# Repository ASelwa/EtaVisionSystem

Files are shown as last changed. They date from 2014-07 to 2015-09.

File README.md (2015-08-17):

**EtaVisionSystem**
===============

This repo contains code and documentation for AeroVelo's Eta speedbike vision system.

It includes code for the Arduino Mega, code for the minimOSD, and some documentation as well as datasheets.

####BRANCHES

The _master_ branch contains the most recent updates.

The _BM-2014_ branch is a quick way to access the code ran at Battle Mountain in September 2014. There were several bugs and issues to be addressed, however it still used at road testing several times leading up to 2015.

The _No-Serial-Printing_ branch contains the code ran at Battle Mountain 2014 without serial printing.

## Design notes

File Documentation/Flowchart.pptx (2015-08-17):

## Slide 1

Start

#include

#define

Variables init

Serial ports opened
Pin modes set
GPS init
SD init
ANT setup
calibrate()

void setup()

void loop()

Periodic While Loop

PERIOD milliseconds hasn’t passed

Increment TIME by PERIOD
Save all data to SD card

New GPS data?

Lat, long, alt moving average.
Displacement, distance calculation
Target power (if not simulation mode)
Toggle()
Send profile
Send mode
Send target speed, speed, simulated speed, distance, displacement, battery info, temperature

GPSLost &&
Time passed > 1000 ms?

Time passed > 7000 ms?

GPSLost = true

Not in Simulation?

Reinitialize GPS

Toggle()
Send profile
Send mode
Send target speed, speed, simulated speed, distance, displacement, battery info, temperature

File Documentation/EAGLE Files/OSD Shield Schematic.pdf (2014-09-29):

2014-09-28 9:58 PM f=1.40 /Users/ASelwa/Documents/GitHub/EtaVisionSystem/Documentation/EAGLE Files/OSD Shield.sch (Sheet: 1/1) VIN P$1 | PIN P$2 | GNDIN P$3 VOUT P$4 | POUT P$5 | GNDOUT P$6
BLK | P$12
GND | P$11
5V | P$10
RX | P$9
TX | P$8

OSD1

GRN P$7

### VIN P$1

### PIN P$2

### GNDIN P$3

### VOUT P$4

### POUT P$5

### GNDOUT P$6

BLK | P$12
GND | P$11
5V | P$10
RX | P$9
TX | P$8

OSD2

GRN P$7

# 1 P$1 2 P$2 3 P$3 SH P$4

CCAM1

# 1 P$1 2 P$2 3 P$3 SH P$4

CCAM2

1 P$1

2 P$2

# 3 P$3 SH P$4

CVOUT1

1 P$1

2 P$2

# 3 P$3 SH P$4

CVOUT2

1 P$1

2 P$2

# 3 P$3 SH P$4

CTEL

TX
RX

DGND

AGND1
VIN1

5V-1

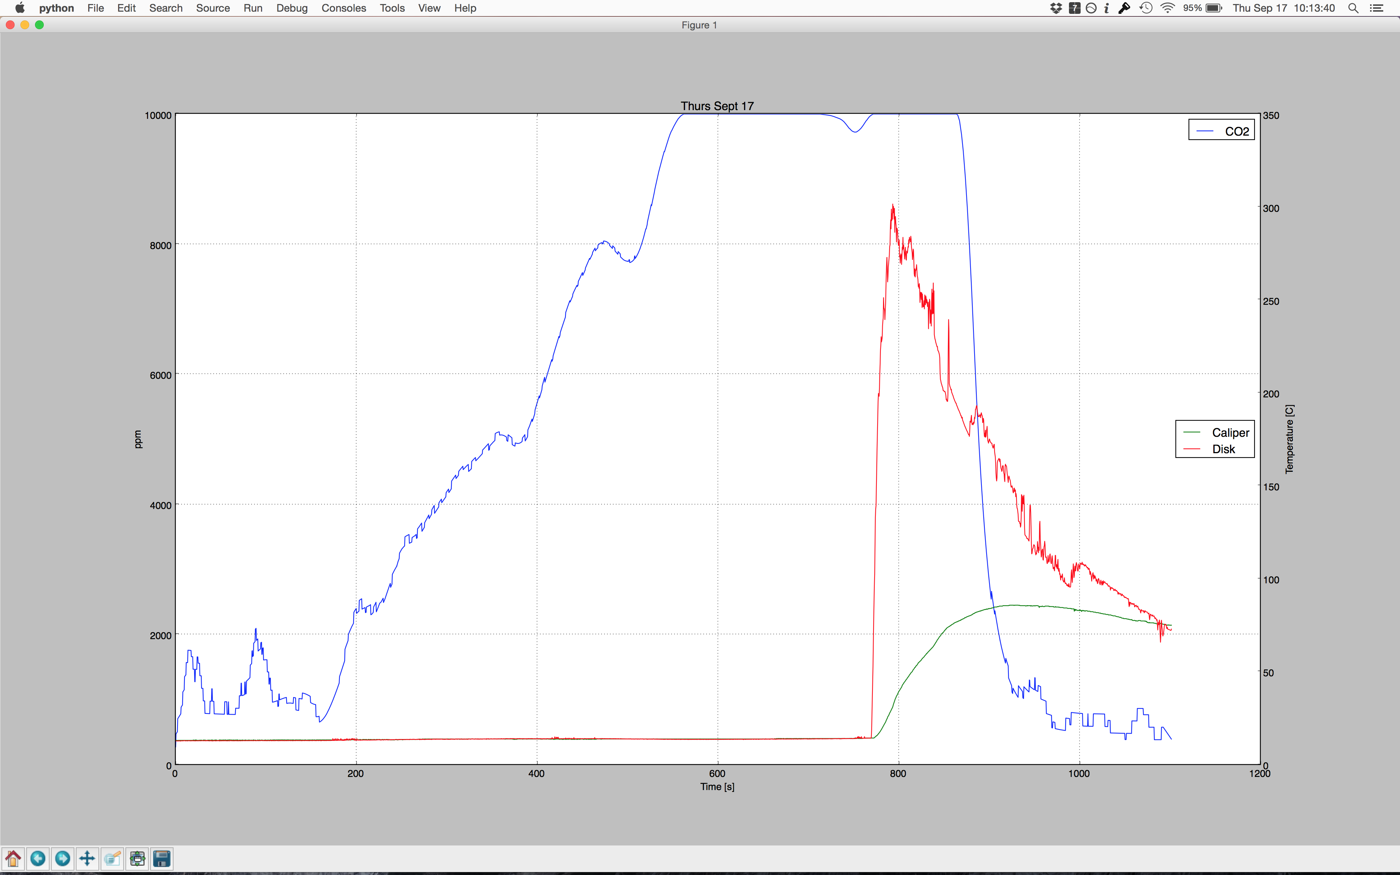
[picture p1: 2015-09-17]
BM 2015 Logs/17 Sept Thursday/CO2 and Temperature.png

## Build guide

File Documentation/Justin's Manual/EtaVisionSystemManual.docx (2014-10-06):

# Eta Vision System Manual

# Introduction to Eta’s Code Structure

The code for Eta’s vision system is divided into two main directories: HPV_ArduinoMega and HPV_OSD. A wealth of standard and custom libraries also support the system’s functioning. With the exception of ArduCam_Max7456 and GPS_UBLOX, there should be no need to modify any of these libraries.

## HPV_ArduinoMega

HPV_ArduinoMega contains files defining the system’s logic. The Arduino streams data from peripheral devices, calculates values of interest, and sends the data to the OSD. Currently, the peripherals supported are:

- ANT+ receiver configured for power pedals, crank torque frequency pedals (e.g. Todd’s SRM), and heart meter
- uBLOX GPS
- Battery meter
- Temperature sensor
- SD card reader

### HPV_ArduinoMega.ino

This is the central processing centre of the system. The setup initializes all the peripherals and pins and calls the calibration function to calibrate the pedals. The main loop receives data from the peripherals, calculates values of interest, and sends these values to the OSD chip via its serial link. In general, data is sent whenever a new message is received from the GPS or the ANT+ receiver. This file also takes care of most of the logging activity, writing values every two seconds to the SD card.

Every time the GPS sends data, or every one second if the GPS is not available, the program will check if the profile toggle button has been pushed. If so, the program will load the next profile.

Notes:

- Most of the variables to display are sent to the OSD when there is a GPS update. Since the GPS may not always be available, there are two lengthy cases containing nearly identical code. One block will execute whenever the GPS updates with a new message while the other block will take over if the Arduino loses its GPS connection. Remember to copy any code you add into both blocks (if applicable).
- The update frequency of logs can be set by changing PERIOD in ANT_interface.h
- Anything related to the START variable seems to have been deprecated

### Ant_interface.cpp

This file contains functions for communication with the antenna. No changes should be necessary to the current code.

### BatteryCheck.ino

This file contains functions to measure the temperature and battery voltage.

### GPS_Func.ino

This file contains logic related to the calculations done with GPS coordinates.

### SD_Func

This file contains functions to perform basic write and read operations.

### TargetSpeed_Func

The functions in this file carry out a variety of tasks not necessarily related to calculating the target speed. The main function is toggle(), which takes care of loading new profiles and switching between real-time and simulation modes. There are also functions to calculate target speed and target power.

# Logging

Currently, there are two logs created for each run of the program. The “LOG” file is a general log that is written to at regular intervals and contains information from all of the peripherals connected. This interval is defined by the PERIOD variable. The contents that are logged can be modified by changing the print commands at the end of loop() in HPV_ArduinoMega.ino. The column headers are specified in setup() of the same file.

The “SLG” file is written to whenever non-duplicate power meter messages are received from the SRM. The contents that are logged can be modified by changing the print commands at the end of loop() in HPV_ArduinoMega.ino. The column headers are specified in setup() of the same file.

Different types of logs from the same run will always have the same number in their file name.

# Programming the OSD

Note: Do not use the OSD configuration GUI. It seems incompatible with the way Eta’s OSD is currently set up and it does not support custom panels.

To program the OSD, connect it to the computer via an FTDI-USB converter. Upload the code through the Arduino IDE, making sure that the board is set to “Arduino Pro or Pro Mini” and the processor is set to “ATMega328 (5V, 16 MHz)”.

## Adding a Display

To add a variable to display onto the screen:

1. Define an ID at the beginning of OSD_SLIP.h and in HPV_ArduinoMega.ino
2. Perform calculations in the main loop of HPV_ArduinoMega.ino
3. Send the value in the main loop via SlipPacketSend()
4. Add an extern variable declaration in OSD_SLIP.cpp
5. Add the regular variable declaration in HPV_OSD.ino
6. Add a case to OSD_SLIP.cpp to extract the value from the buffer and assign it to the variable from steps 4 and 5
7. Add a panel function to OSD_panels_HPV.ino
8. Call the function in writePanels() (also located in OSD_panels_HPV.ino)

## Parameters of Interest

Baud rate: TELEMETRY_SPEED, ArduCAM_OSD.ino

Start-up speed: BOOTTIME, ArduCAM_OSD.ino

# Elevation Calculations

Elevation data is stored using a 2D array of distance and elevation pairs. To keep the data structure small, a few key points along the track were chosen so that linear interpolation could be used for a reasonable estimate of the elevation anywhere along the track. This data can be found near the beginning of simulation.cpp.

The change in elevation cannot be found without first knowing the distance travelled. The distance travelled cannot be known without calculating the net energy added to the bike, but part of this net energy is due to the change in elevation. This circular dependence necessitates an iterative algorithm.

1. First, elevation is ignored. Power, velocity, and distance travelled are calculated.
2. The distance travelled is used to find the change in elevation. Power is recalculated with the power of the elevation change included.
3. Velocity and distance calculations are repeated with the new power value.
4. The elevation change is recalculated. Power is recalculated.
5. Velocity and distance are recalculated.

And so on. Each iteration should result in a closer and closer approximation to the actual distance. The process stops after a maximum of ten iterations, or when the difference in elevation power is less than 1 W, whichever occurs first.

# SRM Data

The SRM sends messages to the antenna at a non-configurable rate of every half a second. While the bike is being pedalled, the contents of the power messages will only update every full revolution. Any messages sent before the next full revolution will be a duplicate of the previous.

# Common Tasks

## Add a speed profile

Create a new file on the SD card called “PF##” where the pound signs are the next unused profile number.

Note: Numbering must begin at 01 and all subsequent profile numbers must be consecutive. The program will stop looking for profiles if it cannot find a profile with the next consecutive number.

The first argument is the profile name. The name should be a maximum length of 10 characters and cannot contain spaces. A profile name longer than the limit will be truncated when it is displayed. The next six arguments are the coefficients for the polynomial approximation in order of highest power (degree 6) to lowest (constant term). Each argument must be separated by a space.

## Change the target power profile

The target power profile currently uses a simple linear equation to find the target value. The starting and ending targets are defined as preprocessor variables POWER_START and POWER_PRE_SPRINT. To change the method of calculation, modify functions calcPower() and calcDisplacePower()in TargetSpeed_Func.ino.

## Set the finish line coordinates

Edit the file on the SD card called “FinCoord.txt”. The first argument is the latitude (in degrees), the second is the longitude (in degrees), and the third is the altitude (in metres). Each argument must be separated by a space.

# Troubleshooting

## No calibration data is received (display will only read “Waiting”)

This is likely a problem with the antenna. If certain antenna pins short, the antenna will not work until the short is removed and the antenna is reinitialized.

1. Unplug and plug the antenna. Ensure nothing is shorting the pins. Restart the program.
2. Replace the antenna with the backup.
3. Measure the three baud rate selection pins while the Arduino is powered and ensure their logic levels match the ones specified for the baud rate used in the program (see Antenna Datasheet.pdf).
4. Comment out the call to calibrate() in HPV_ArduinoMega’s setup(). Run the program using the serial monitor. If there are no ANT+ messages received after the ANT+ setup has complete, the problem is definitely with the antenna.

At this point, if the problem persists, switch to a back-up system and try again later.

## Power, cadence, distance and heart rate displays freeze

These are all dependent on the antenna. See above.

The power meter will automatically shut off after a specified period of no activity (around 2 minutes). After this time, the program will stop calculating new values.

## GPS not available

1. Check that the device is getting power (red LED should be lit).
2. Restart the system.
3. Try the old GPS. If it works, the new one is likely damaged or misconfigured.
4. Start U-Center and plug the GPS into the computer. Ensure the correct messages are being sent, the baud rate is configured correctly, and the message rate is reasonable. (Refer to the GPS configuration section). If U-Center can’t communicate with the GPS, it may be damaged. Use the backup GPS.

## OSD text flickers on screen

1. Ensure the OSD wire connections are stable and nothing is touching the OSD chip.
2. Ensure any calls to OSD.clear() are controlled appropriately (do not attempt to call the function without a time delay).
3. Ensure the display and OSD chip are both set on NTSC mode (see OSD section).

## A Value jumps to an extremely large number

This is most likely caused by a division by zero (and not some hidden modification of variable values or overwriting memory where it shouldn’t be overwritten). Check any calculations related to the variable and ensure that undefined operations cannot occur.

# Known Issues

## Arduino peripherals (e.g. GPS) stop working after uploading new code

### Cases

Uploading the code using Justin’s laptop running Arduino 1.5.5 (older, no longer supported), the code works as expected. When identical code is uploaded using Steven’s laptop running Arduino 1.0.5 (newest version of the 1.0 series), the GPS will not initialize.

### Analysis

Compiling on different versions of the IDE (or possibly on different computers) may break the code. In the given case, it seems to be related to the pre-processor variables that detect what Arduino board the GPS is running on (see GPS_UBLOX_Class::Init in GPS_UBLOX.cpp). More testing is required to determine the cause of this. We suspect this problem can be fixed by removing the pre-processor variables, forcing the code to assume an ATMega board.

## Serial Buffer Overflow – Solved

### Cases

The ANT+ serial will occasionally receive corrupted messages that can be up to 255 bytes long. This is highly dangerous, as the ANT+ buffer is only large enough to support messages up to 64 bytes. (In theory, no messages should be above 9 bytes in length.) Additional bytes will write into adjacent memory, overwriting any variables that may be stored there. This behaviour is completely undefined.

### Analysis and Solution

It seems as though these large, “cancerous” messages are actually composed of a few 9-byte messages repeated many times.

The code relies on a sync byte (0xA4 or 0xA5, although in practice it always seems to be 0xA4 and the code ignores 0xA5 for extra security) to identify the beginning of a message. The program is usually fine at synchronizing with the ANT+ serial, but sometimes it misinterprets a 0xA4 that is part of a message payload to be the sync byte of a new message. It will then assume that the following byte is the message length, causing this error.

A check has been put into place in receiveANT() of ANT_interface.cpp to discard the message as soon as the message length byte is greater than 9. This means an overflow should never occur with antBuffer.

## SD card contains strange files

### Cases

The SD card is susceptible to corruption. Our testing has shown the following cases:

- A file with the name “ . ■” that Windows Explorer thinks takes up around 4GB of drive space. Pulling up the Properties window, however, shows that it is an empty (0B) file.
- A “ghost” file that takes up no space and cannot be deleted (deleting is successful, but refreshing the directory will cause the file to reappear).

### Analysis

This problem likely stems from the fact that the SD card can be removed at any time, including during a write operation. There is a library function to initialize the SD card, but no function to disconnect safely from the SD.

## Simulation – Solved???

### Cases

The simulate function risks dividing by 0, which may cause undefined behaviour. On the Arduino, variables will become infinity or NaN (not a number). On the OSD, they may display as garbage values. As soon as velocity and/or distance become either of these values, they will not recover.

### Analysis and Solution

Steps have already been taken to prevent floating point calculations from ruining the program. Guards are present in many simulate() calculations to attempt to handle unreasonable values, and simulate() includes a final check that will abort the current iteration without updating any of the values if any variables become infinite or undefined. Recent testing and logging have not revealed any problems with infinite or undefined variables; however, they have also not revealed any cases in which undefined variables were actually caught and handled gracefully. Therefore, it is not known if the current security measures are effective.

## Shorting – Solved

### Cases

When standoffs were still installed on the box and the Arduino was powered without properly locking it in place, the board heated rapidly, becoming hot enough to burn the epoxy.

### Analysis and Solution

We speculate that one of the standoffs came into contact with the Vin pin on the bottom of the Arduino and shorted it by conducting across the carbon fibre board. Never run the circuit while the Arduino is sitting on a conductive surface.

The nature of the problem could have been avoided by replacing the standoffs with foam or another insulating material. The box is now taped to prevent this from happening in the future.

## OSD shows rapidly flashing garbage numbers in place of meaningful ones – Solved

### Cases

Whenever a value is rapidly written to the OSD (no explicit time delay between writes), the value flickers to random numbers.

### Analysis and solution

The reason for this is unknown, but the problem can be solved by ensuring an adequate delay between write operations.

# Miscellaneous Notes

## Forward Declarations

- Arduino automatically generates forward declarations for functions. It is therefore never necessary to do so for most functions.
  - Exceptions include functions with function pointers as parameters, default arguments, and functions declared in a namespace or class. Manual declarations will be necessary.

## Multi-file Programs

- Arduino (.pde and .ino) files do not work like regular .c or .cpp files. The Arduino compiler concatenates all Arduino files in the same folder into one compilation unit. (C and C++ files are treated as separate compilation units.) The concatenation begins with the main file (which shares the folder name), followed by the other Arduino files in alphabetical order (not verified, widely accepted). Therefore, for Arduino files in the same folder:
  - Include statements are only necessary in the main file
  - The static keyword will not restrict variable scope to only the local Arduino file
  - Global variables in one file do not have to be declared as extern in another to be used
  - Regular variable scope rules still apply. A global variable declared in “B.ino” cannot be referenced in “A.ino” because A will concatenated before B.

## SD Card

- Arduino cannot log files with names longer than 8 characters (FAT 8.3 standard (http://arduino.cc/en/Reference/SDCardNotes)).
- Arduino capitalizes all letters in file names when creating a file.

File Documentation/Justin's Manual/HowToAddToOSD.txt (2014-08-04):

To add a variable to display onto the screen:

1. Define an ID in OSD_SLIP.h and in HPV_ArduinoMega
2. Perform calculations/read from ANT in main loop of HPV_ArduinoMega
3. Send value in main loop via SlipPacketSend
4. Add an extern variable declaration in OSD_SLIP.cpp
5. Add the regular variable declaration in HPV_OSD
6. Add a case to OSD_SLIP.cpp to extract the value from the buffer and assign it to the variable from steps 4/5
7. Add a panel function to OSD_panels_HPV
8. Call the function in writePanels() (also located in OSD_panels_HPV)

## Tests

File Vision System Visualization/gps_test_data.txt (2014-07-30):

Index	UTC	SoG	Lat	Lon
Unit	time date	m/s	°	°
Count	1344	1344	1344	1344
Age	0	0	0	0
Current	23:08:41.000 07/29/2014	0.01	43.551496	-79.663104
Minimum	22:46:18.000 07/29/2014	0.00	43.535137	-79.663115
Maximum	23:08:41.000 07/29/2014	34.11	43.658515	-79.393437
Average		14.63	43.589041	-79.582394
Deviation		12.37	0.046276	0.084452
0	22:46:18.000 07/29/2014	0.00	43.658515	-79.393437
1	22:46:19.000 07/29/2014	0.00	43.658515	-79.393437
2	22:46:20.000 07/29/2014	0.00	43.658515	-79.393437
3	22:46:21.000 07/29/2014	0.00	43.658515	-79.393437
4	22:46:22.000 07/29/2014	0.00	43.658515	-79.393437
5	22:46:23.000 07/29/2014	0.00	43.658515	-79.393437
6	22:46:24.000 07/29/2014	0.00	43.658515	-79.393437
7	22:46:25.000 07/29/2014	0.00	43.658515	-79.393437
8	22:46:26.000 07/29/2014	0.00	43.658515	-79.393437
9	22:46:28.000 07/29/2014	0.00	43.658515	-79.393437
10	22:46:29.000 07/29/2014	0.00	43.658515	-79.393437
11	22:46:30.000 07/29/2014	0.00	43.658515	-79.393437
12	22:46:31.000 07/29/2014	0.00	43.658515	-79.393437
13	22:46:32.000 07/29/2014	0.00	43.658515	-79.393437
14	22:46:33.000 07/29/2014	0.00	43.658515	-79.393437
15	22:46:34.000 07/29/2014	0.00	43.658515	-79.393437
16	22:46:35.000 07/29/2014	0.00	43.658515	-79.393437
17	22:46:36.000 07/29/2014	0.00	43.658515	-79.393437
18	22:46:37.000 07/29/2014	0.00	43.658515	-79.393437
19	22:46:38.000 07/29/2014	0.00	43.658515	-79.393437
20	22:46:39.000 07/29/2014	0.00	43.658515	-79.393437
21	22:46:40.000 07/29/2014	0.00	43.658515	-79.393437
22	22:46:41.000 07/29/2014	0.00	43.658515	-79.393437
23	22:46:42.000 07/29/2014	0.00	43.658515	-79.393437
24	22:46:43.000 07/29/2014	0.00	43.658515	-79.393437
25	22:46:44.000 07/29/2014	0.00	43.658515	-79.393437
26	22:46:45.000 07/29/2014	0.00	43.658515	-79.393437
27	22:46:46.000 07/29/2014	0.00	43.658515	-79.393437
28	22:46:47.000 07/29/2014	0.00	43.658515	-79.393437
29	22:46:48.000 07/29/2014	0.00	43.658515	-79.393437
30	22:46:49.000 07/29/2014	0.00	43.658515	-79.393437
31	22:46:50.000 07/29/2014	0.00	43.658515	-79.393437
32	22:46:51.000 07/29/2014	0.00	43.658515	-79.393437
33	22:46:52.000 07/29/2014	0.00	43.658515	-79.393437
34	22:46:53.000 07/29/2014	0.00	43.658515	-79.393437
35	22:46:54.000 07/29/2014	0.00	43.658515	-79.393437
36	22:46:55.000 07/29/2014	0.00	43.658515	-79.393437
37	22:46:56.000 07/29/2014	0.00	43.658515	-79.393437
38	22:46:57.000 07/29/2014	0.00	43.658515	-79.393437
39	22:46:58.000 07/29/2014	0.00	43.658515	-79.393437
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

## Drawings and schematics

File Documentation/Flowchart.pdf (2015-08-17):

# void setup()

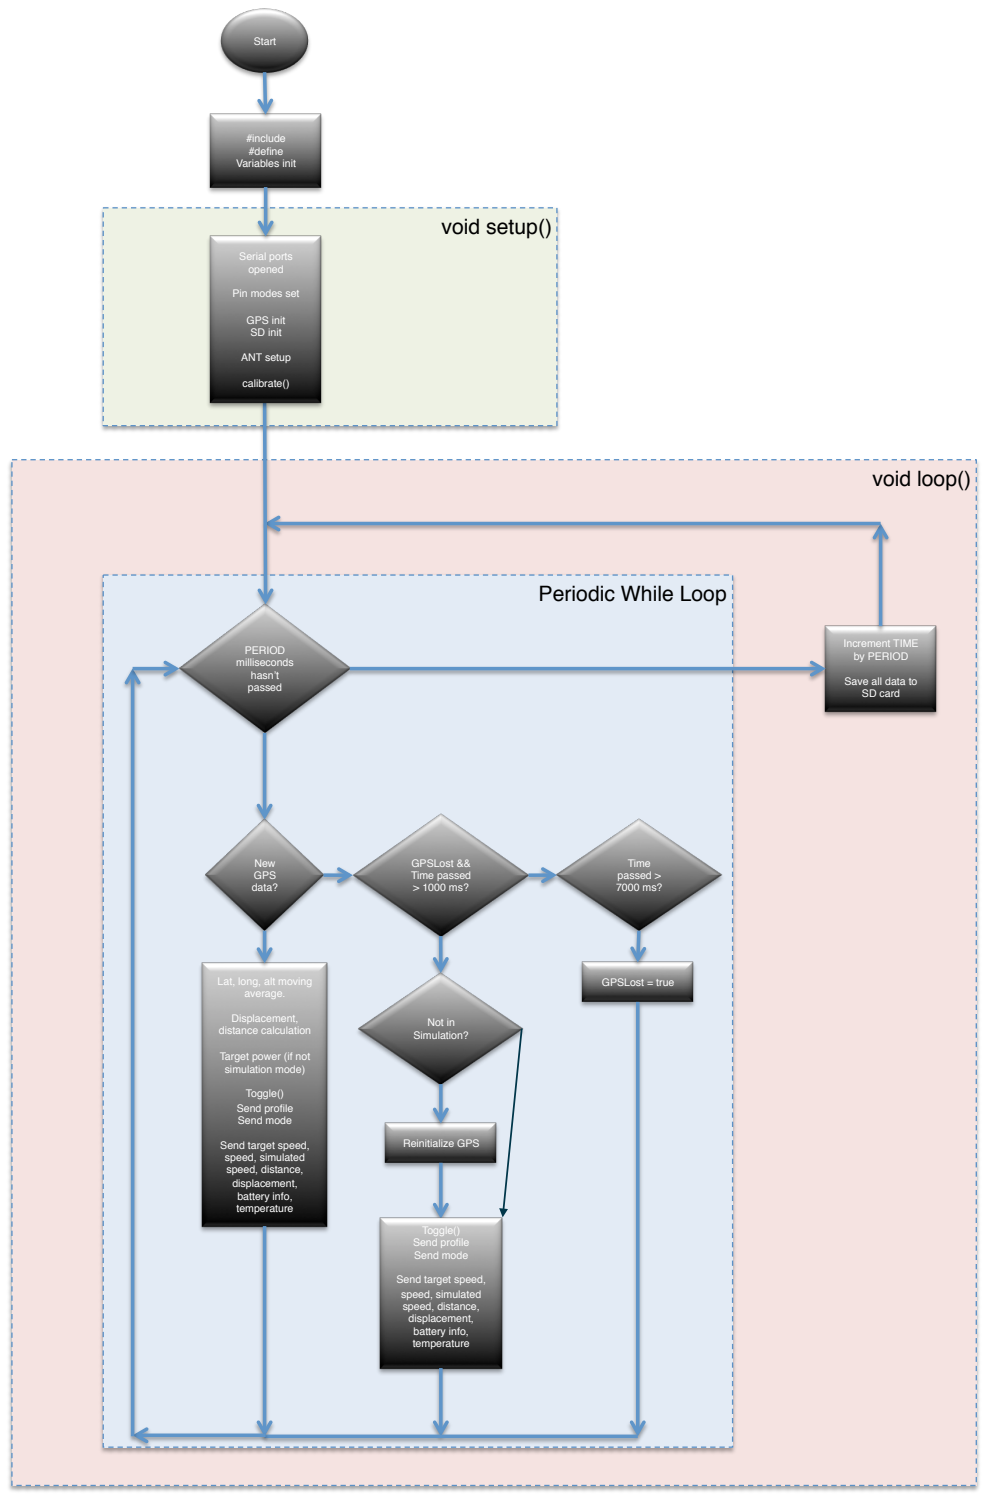
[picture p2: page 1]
void loop(); New GPS data?; GPSLost && Time passed > 1000 ms?; Not in Simulation?; Time passed > 7000 ms?; GPSLost = true; Reinitialize GPS; Toggle() Send profile Send mode; Displacement, distance calculation; Increment TIME by PERIOD; PERIOD milliseconds hasn’t passed; #include #define Variables init; Serial ports opened; GPS init SD init; ANT setup; calibrate(); Start

Pin modes set

Periodic While Loop

Save all data to
SD card

Lat, long, alt moving
average.

Target power (if not
simulation mode)

Send target speed,
speed, simulated
speed, distance,
displacement,
battery info,
temperature

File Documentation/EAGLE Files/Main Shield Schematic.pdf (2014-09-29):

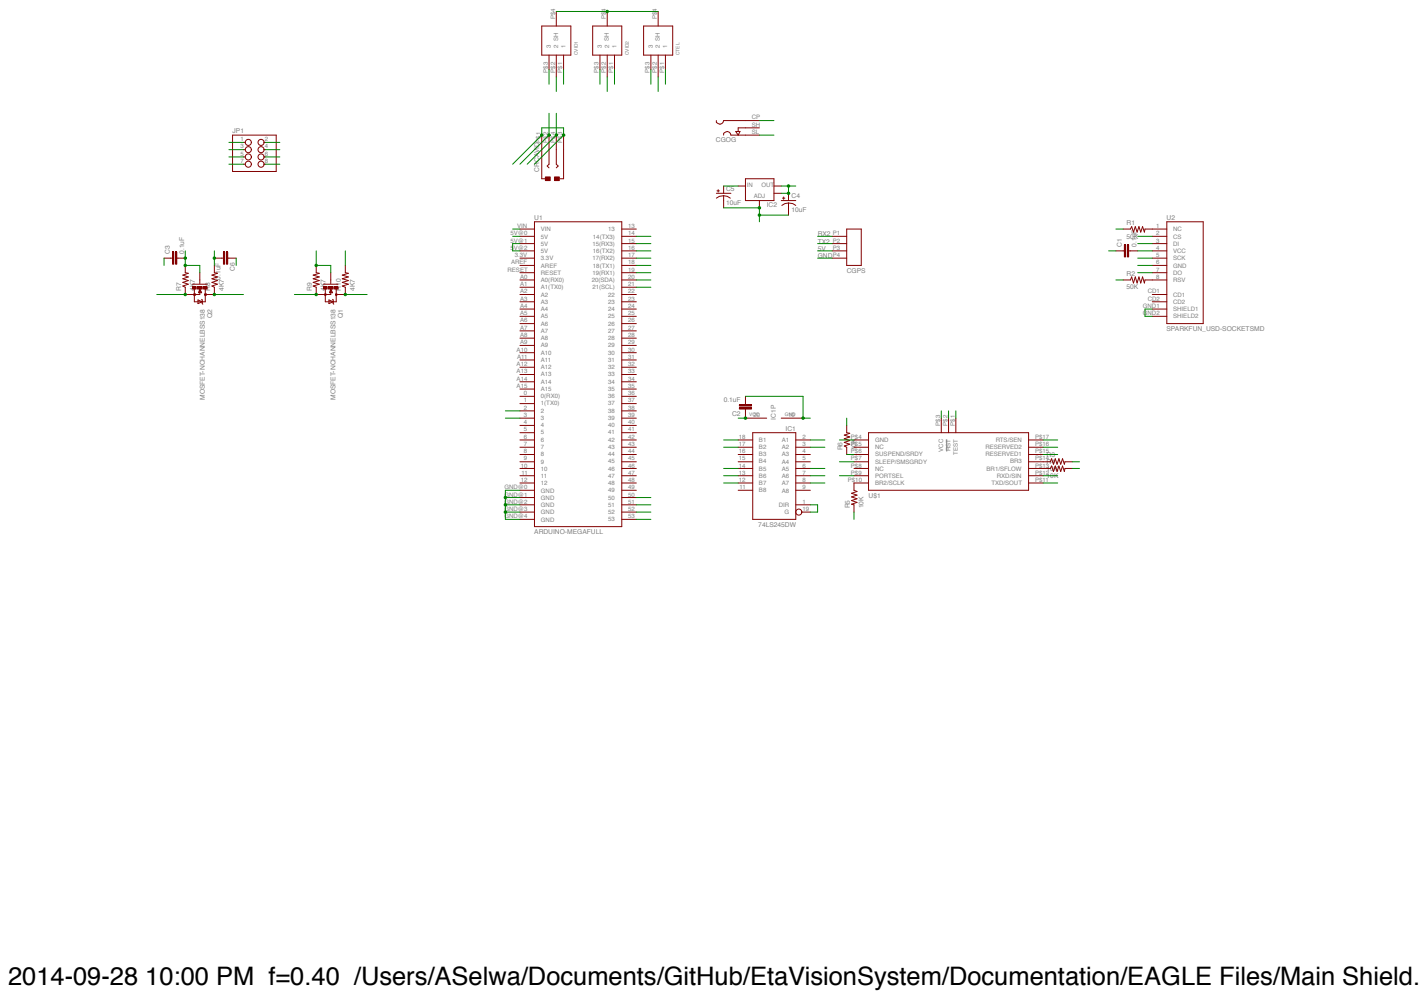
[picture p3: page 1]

2014-09-28 10:00 PM f=0.40 /Users/ASelwa/Documents/GitHub/EtaVisionSystem/Documentation/EAGLE Files/Main Shield.sch (Sheet: 1/1)

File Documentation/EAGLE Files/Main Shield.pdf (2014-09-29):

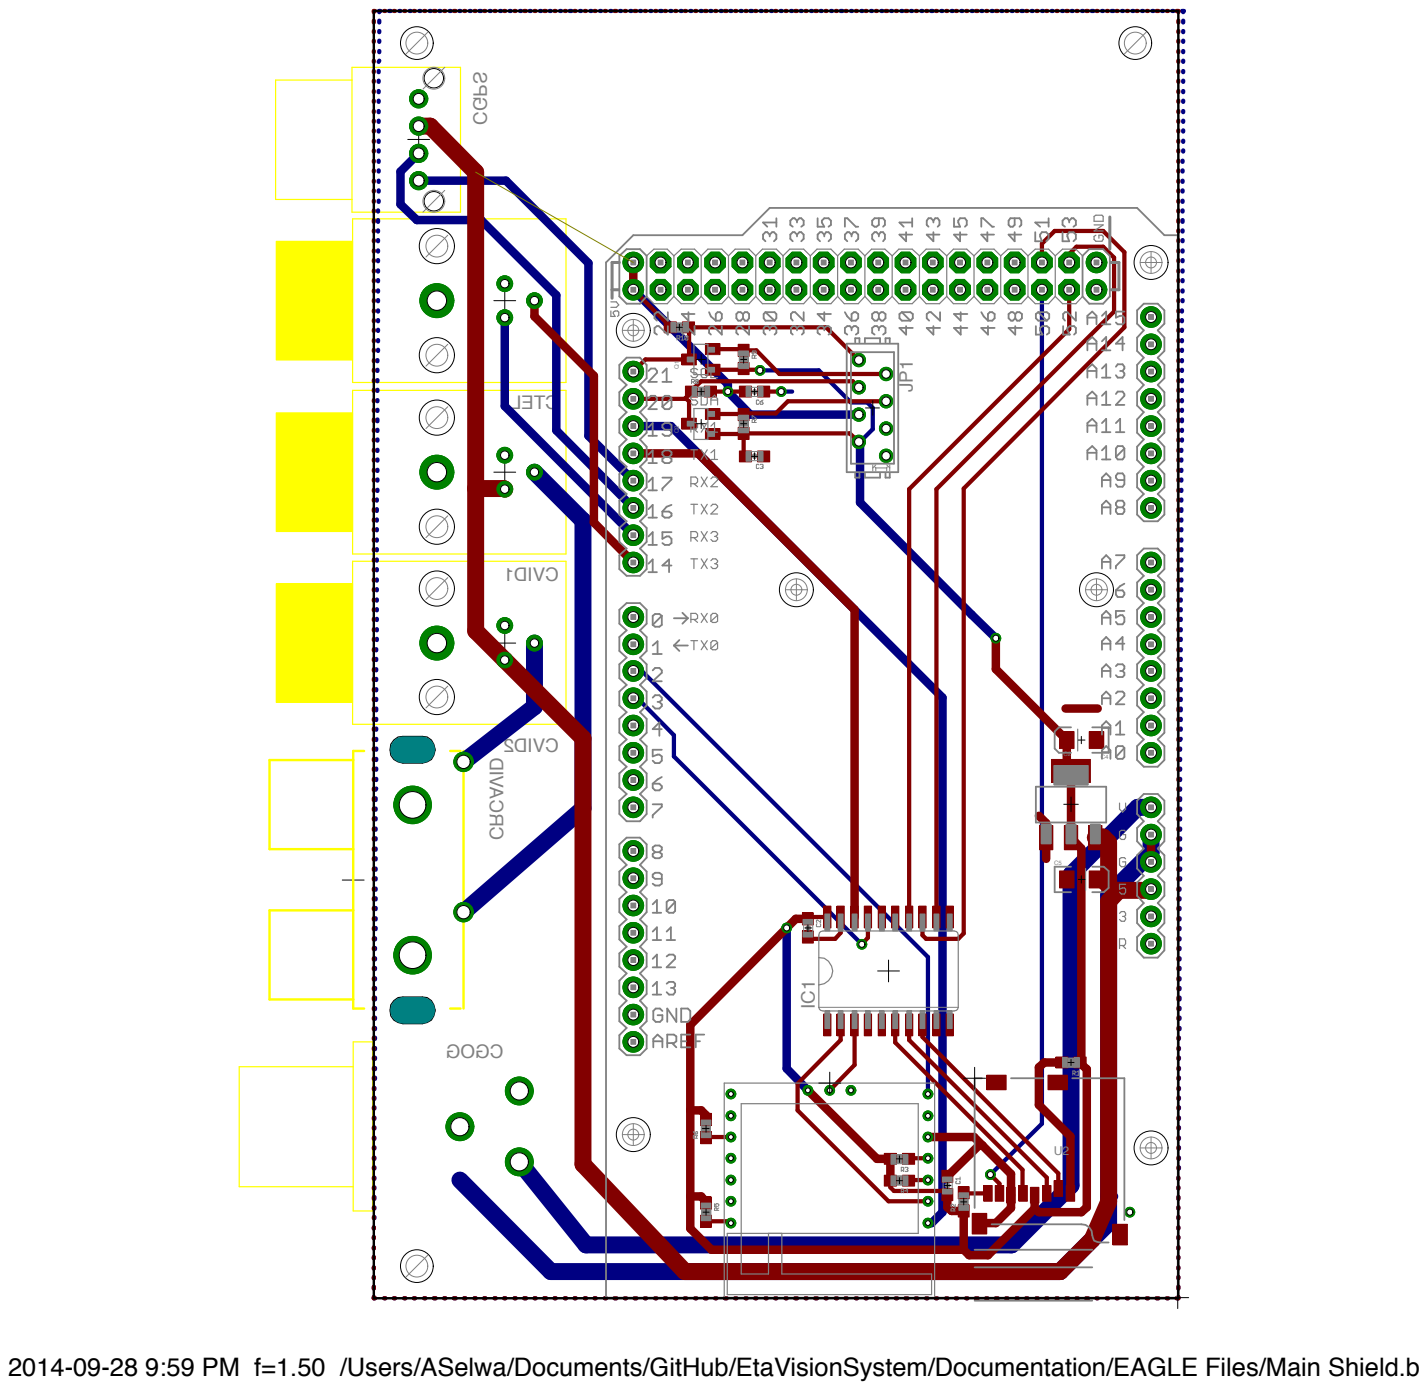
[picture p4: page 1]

2014-09-28 9:59 PM f=1.50 /Users/ASelwa/Documents/GitHub/EtaVisionSystem/Documentation/EAGLE Files/Main Shield.brd

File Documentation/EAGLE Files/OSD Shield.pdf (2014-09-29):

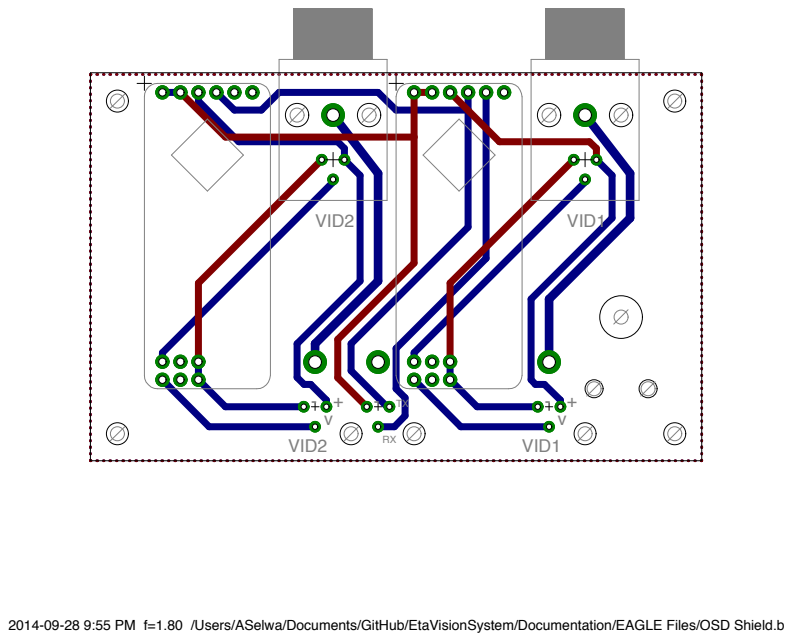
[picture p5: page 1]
VID1; VID2

2014-09-28 9:55 PM f=1.80 /Users/ASelwa/Documents/GitHub/EtaVisionSystem/Documentation/EAGLE Files/OSD Shield.brd

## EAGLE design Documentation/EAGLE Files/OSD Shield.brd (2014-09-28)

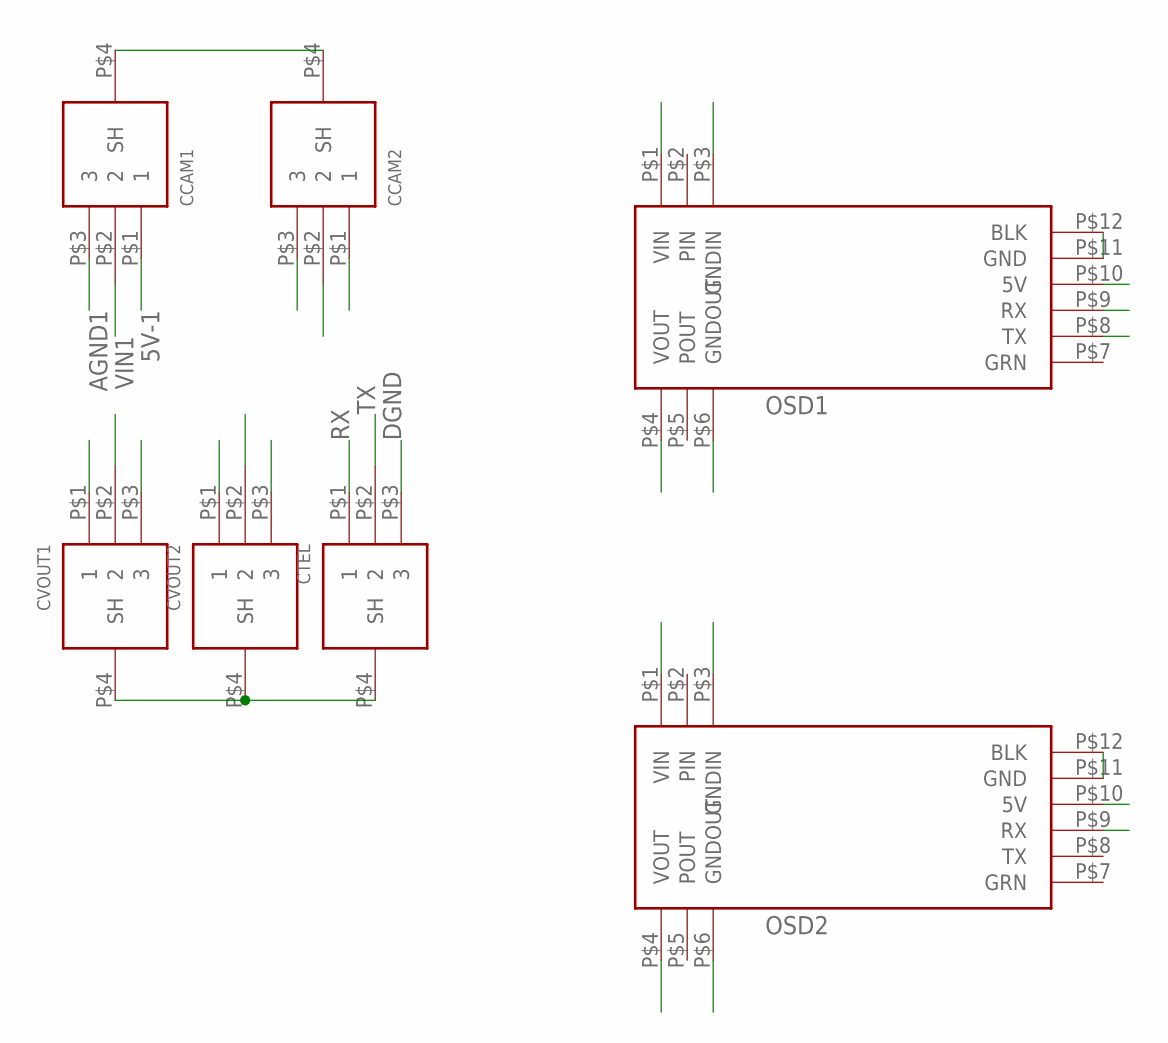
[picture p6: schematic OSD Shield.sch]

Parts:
CCAM1, CCAM2: TRA3M
CTEL: TRA3MBARE; TRA3M-BARE
CVOUT1, CVOUT2: TRA3MBARE; TRA3M-BARE
OSD1, OSD2: MINIM-OSD

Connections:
5V-1: CCAM1.P$1 (1), CVOUT1.P$1 (1), OSD1.P$10 (5V)
5V-2: CCAM2.P$1 (1), CVOUT2.P$1 (1), OSD2.P$10 (5V)
AGND1: CCAM1.P$3 (3), CVOUT1.P$3 (3), OSD1.P$3 (GNDIN), OSD1.P$6 (GNDOUT)
AGND2: CCAM2.P$3 (3), CVOUT2.P$3 (3), OSD2.P$3 (GNDIN), OSD2.P$6 (GNDOUT)
DGND: CTEL.P$3 (3), OSD1.P$11 (GND), OSD1.P$12 (BLK), OSD2.P$11 (GND), OSD2.P$12 (BLK)
RX: CTEL.P$1 (1), OSD1.P$9 (RX), OSD2.P$9 (RX)
SHLD: CCAM1.P$4 (SH), CCAM2.P$4 (SH), CTEL.P$4 (SH), CVOUT1.P$4 (SH), CVOUT2.P$4 (SH)
TX: CTEL.P$2 (2), OSD1.P$8 (TX)
VIN1: CCAM1.P$2 (2), OSD1.P$1 (VIN)
VIN2: CCAM2.P$2 (2), OSD2.P$1 (VIN)
VOUT1: CVOUT1.P$2 (2), OSD1.P$4 (VOUT)
VOUT2: CVOUT2.P$2 (2), OSD2.P$4 (VOUT)

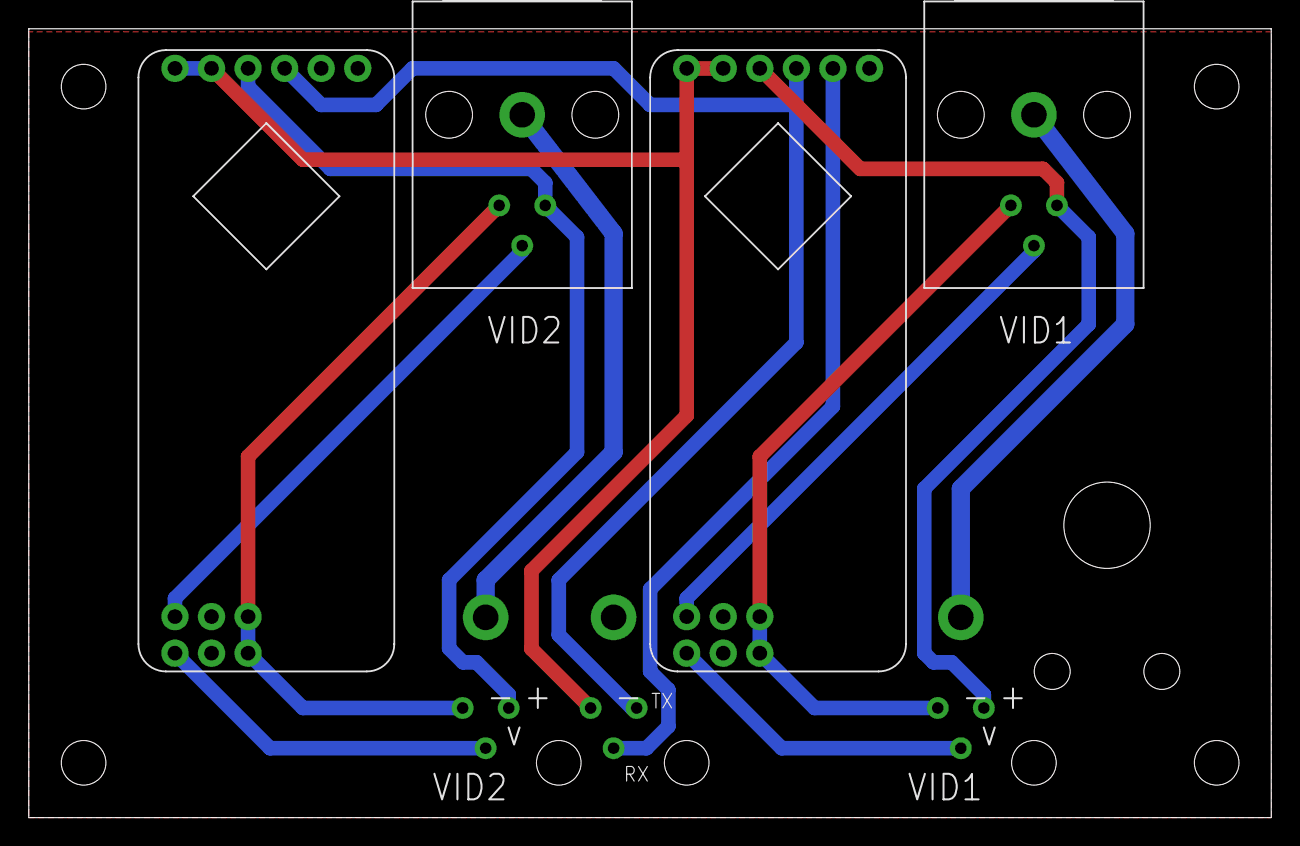
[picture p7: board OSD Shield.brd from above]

Board: 2 copper layers, 86.3 x 54.8 mm, 7 parts (0 on the bottom side), 12 nets.

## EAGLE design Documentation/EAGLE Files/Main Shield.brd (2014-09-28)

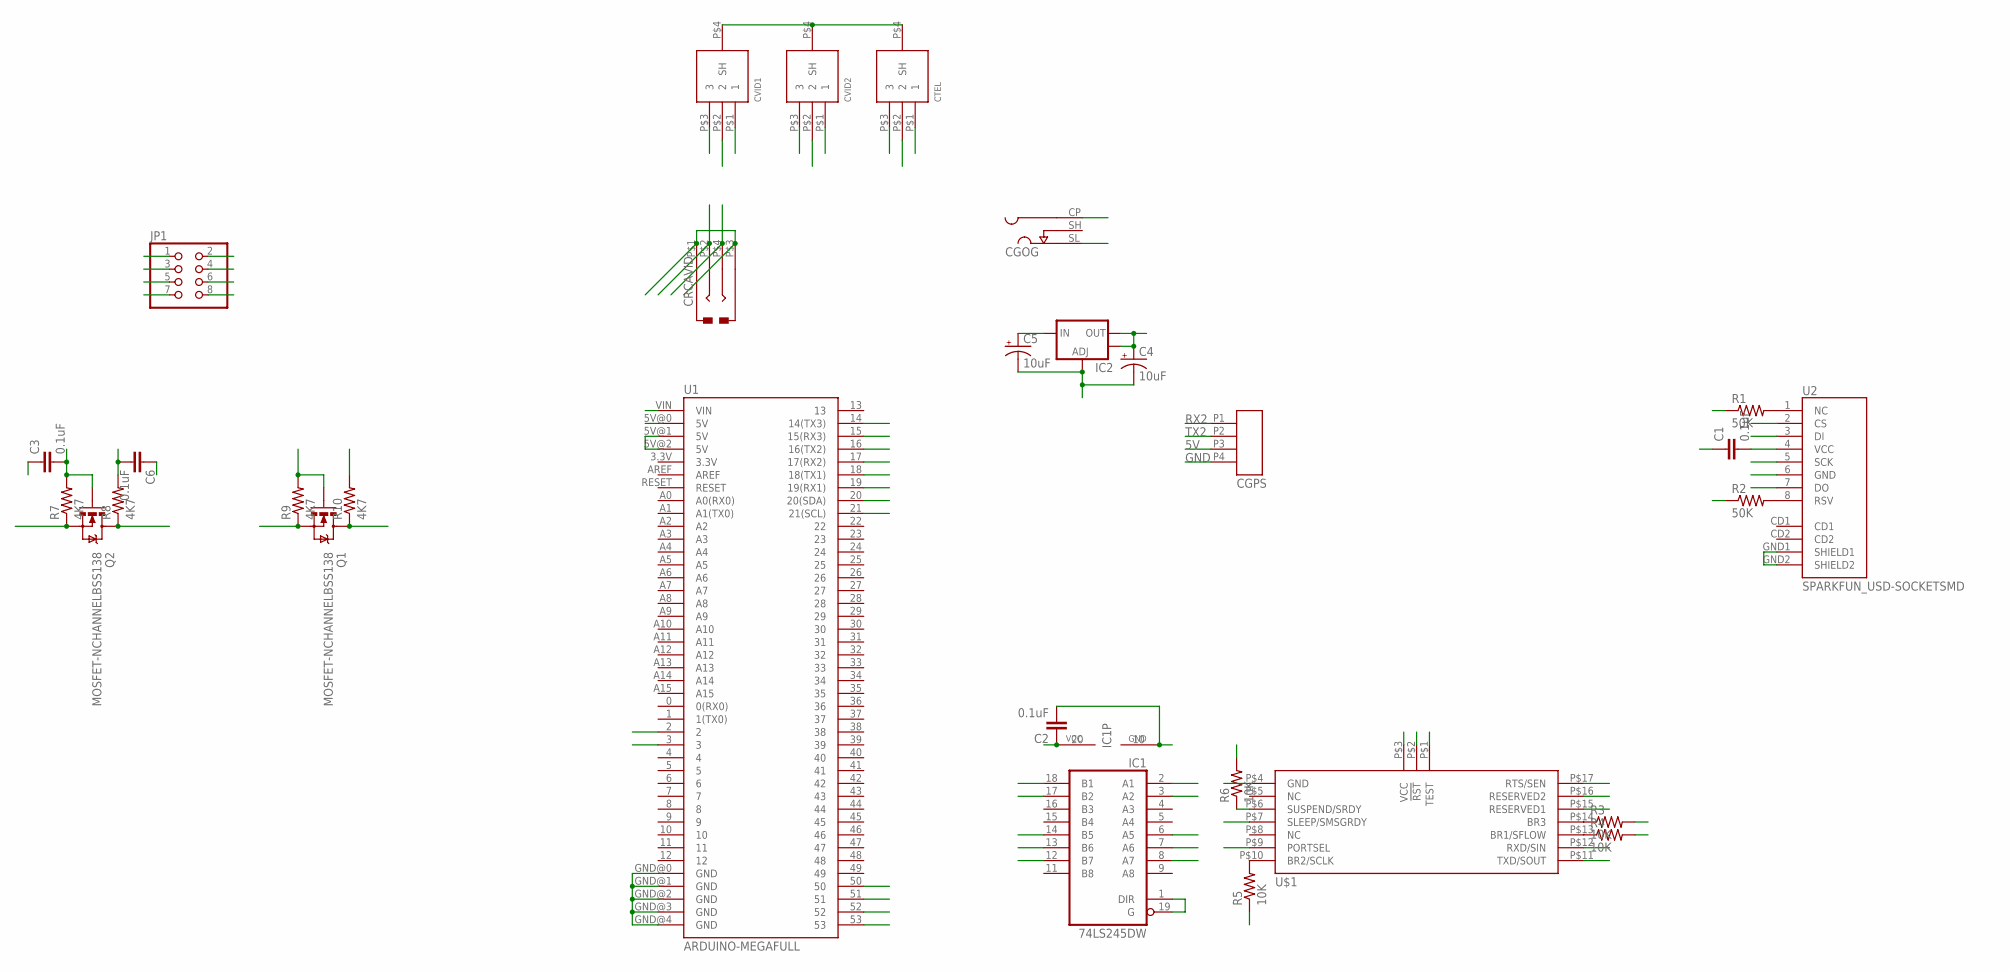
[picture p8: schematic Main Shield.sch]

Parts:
C1, C2, C3, C6: 0.1uF; 0603-CAP
C4, C5: 10uF; EIA3216
CGOG: L722RAS
CGPS: TRAPC4MSX
CRCAVID: RCJ-2123
CTEL: TRA3M
CVID1, CVID2: TRA3M
IC1: 74LS245DW; SO20W
IC2: V_REG_LM1117SOT223; SOT223
JP1: PINHD-2X04_MICROMATCH; MICROMATCH-8
Q1, Q2: MOSFET-NCHANNELBSS138; SOT23
R1, R2: 50K; 0603-RES
R3, R4, R5, R6: 10K; 0603-RES
R7, R8, R9, R10: 4K7; 0603-RES
U1: ARDUINO-MEGAFULL; ARDUINO_MEGA
U2: SPARKFUN_USD-SOCKETSMD; SPARKFUN_MICRO-SD-SOCKET-PP
U$1: ANTAP281MXIB

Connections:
3V3: C1.2, C2.1, C3.2, C4.A (+), IC1.20 (VCC), IC2.2 (OUT), IC2.4 (OUT), JP1.2, Q1.1 (G), Q2.1 (G), R1.1, R2.1, R3.2, R4.2, R5.1, R6.2, R7.2, R9.2, U2.4 (VCC), U$1.P$3 (VCC)
5V: C5.A (+), C6.2, CGPS.P3, CVID1.P$1 (1), CVID2.P$1 (1), IC2.3 (IN), JP1.4, R8.2, R10.2, U1.5V@0 (5V), U1.5V@1 (5V), U1.5V@2 (5V)
!RST!ANT: IC1.3 (A2), U$1.P$2 (!RST!)
!RST!ANT5V: IC1.17 (B2), U1.3
CSMMC: IC1.8 (A7), U2.2 (CS)
DIMMC: IC1.7 (A6), U2.3 (DI)
DOMMC: U1.50, U2.7 (DO)
GND: C1.1, C2.2, C3.1, C4.C (-), C5.C (-), C6.1, CGOG.SL (SLEEVE), CGPS.P4, CRCAVID.P$1, CRCAVID.P$3, CTEL.P$3 (3), CTEL.P$4 (SH), CVID1.P$3 (3), CVID1.P$4 (SH), CVID2.P$3 (3), CVID2.P$4 (SH), IC1.1 (DIR), IC1.10 (GND), IC1.19 (G), IC2.1 (ADJ), JP1.1, JP1.3, U1.GND@0 (GND), U1.GND@1 (GND), U1.GND@2 (GND), U1.GND@3 (GND), U1.GND@4 (GND), U2.6 (GND), U2.GND1 (SHIELD1), U2.GND2 (SHIELD2), U$1.P$1 (TEST), U$1.P$4 (GND), U$1.P$7 (SLEEP/SMSGRDY), U$1.P$9 (PORTSEL), U$1.P$15 (RESERVED1), U$1.P$16 (RESERVED2)
MOSI: IC1.13 (B6), U1.51
unnamed: R1.2, U2.1 (NC)
unnamed: R2.2, U2.8 (RSV)
unnamed: R3.1, U$1.P$14 (BR3)
unnamed: R4.1, U$1.P$13 (BR1/SFLOW)
unnamed: R5.2, U$1.P$10 (BR2/SCLK)
unnamed: R6.1, U$1.P$6 (SUSPEND/SRDY)
RTSANT: U1.2, U$1.P$17 (RTS/SEN)
RX2: CGPS.P1, U1.17 (17(RX2))
RXANT: IC1.2 (A1), U$1.P$12 (RXD/SIN)
RXOSD: CTEL.P$2 (2), U1.14 (14(TX3))
SCK: IC1.14 (B5), U1.52
SCKMMC: IC1.6 (A5), U2.5 (SCK)
SCL3V3: JP1.7, Q1.2 (S), R9.1
SCL5V: JP1.8, Q1.3 (D), R10.1, U1.21 (21(SCL))
SDA3V3: JP1.5, Q2.2 (S), R7.1
SDA5V: JP1.6, Q2.3 (D), R8.1, U1.20 (20(SDA))
SS: IC1.12 (B7), U1.53
TX1: IC1.18 (B1), U1.18 (18(TX1))
TX2: CGPS.P2, U1.16 (16(TX2))
TXANT: U1.19 (19(RX1)), U$1.P$11 (TXD/SOUT)
TXOSD: CTEL.P$1 (1), U1.15 (15(RX3))
VBAT: CGOG.CP (CENTRE), U1.VIN
VID1: CRCAVID.P$2, CVID1.P$2 (2)
VID2: CRCAVID.P$4, CVID2.P$2 (2)

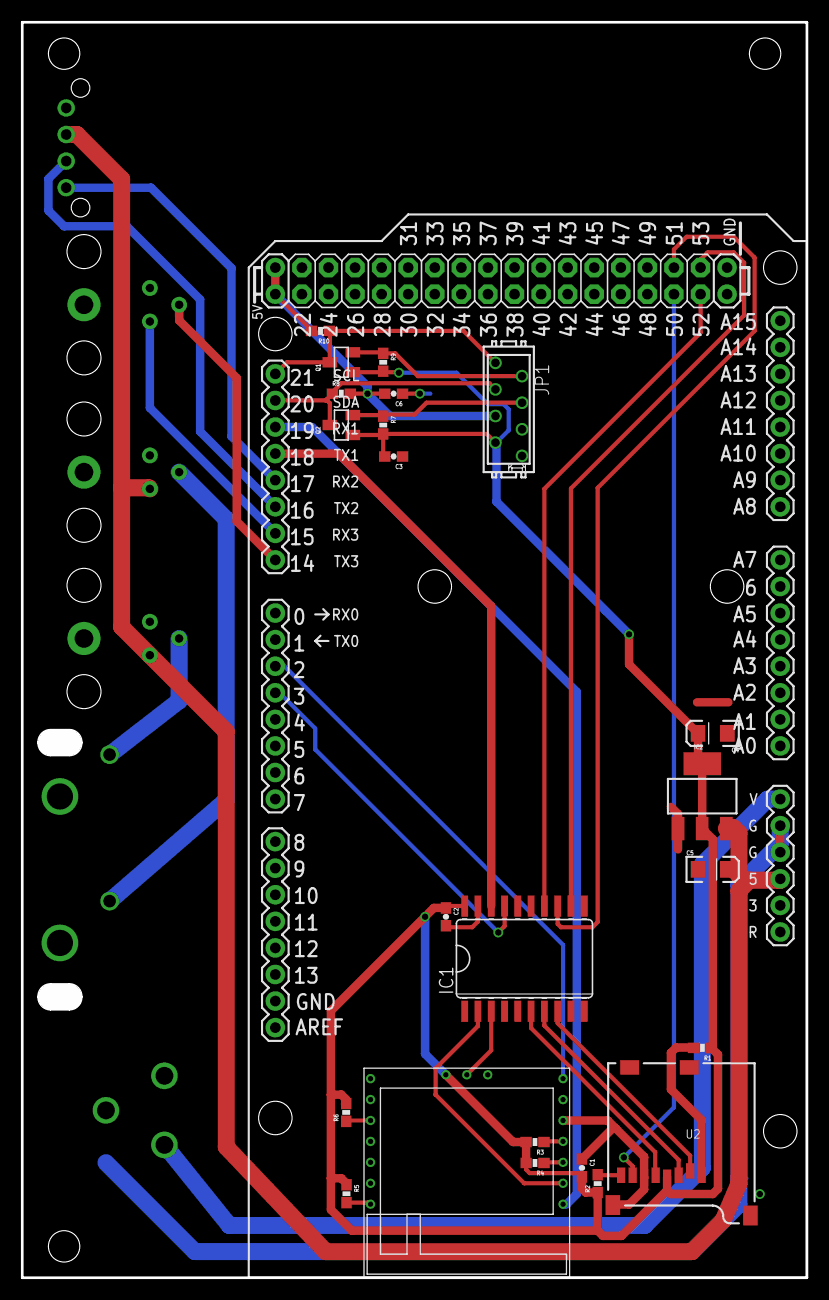
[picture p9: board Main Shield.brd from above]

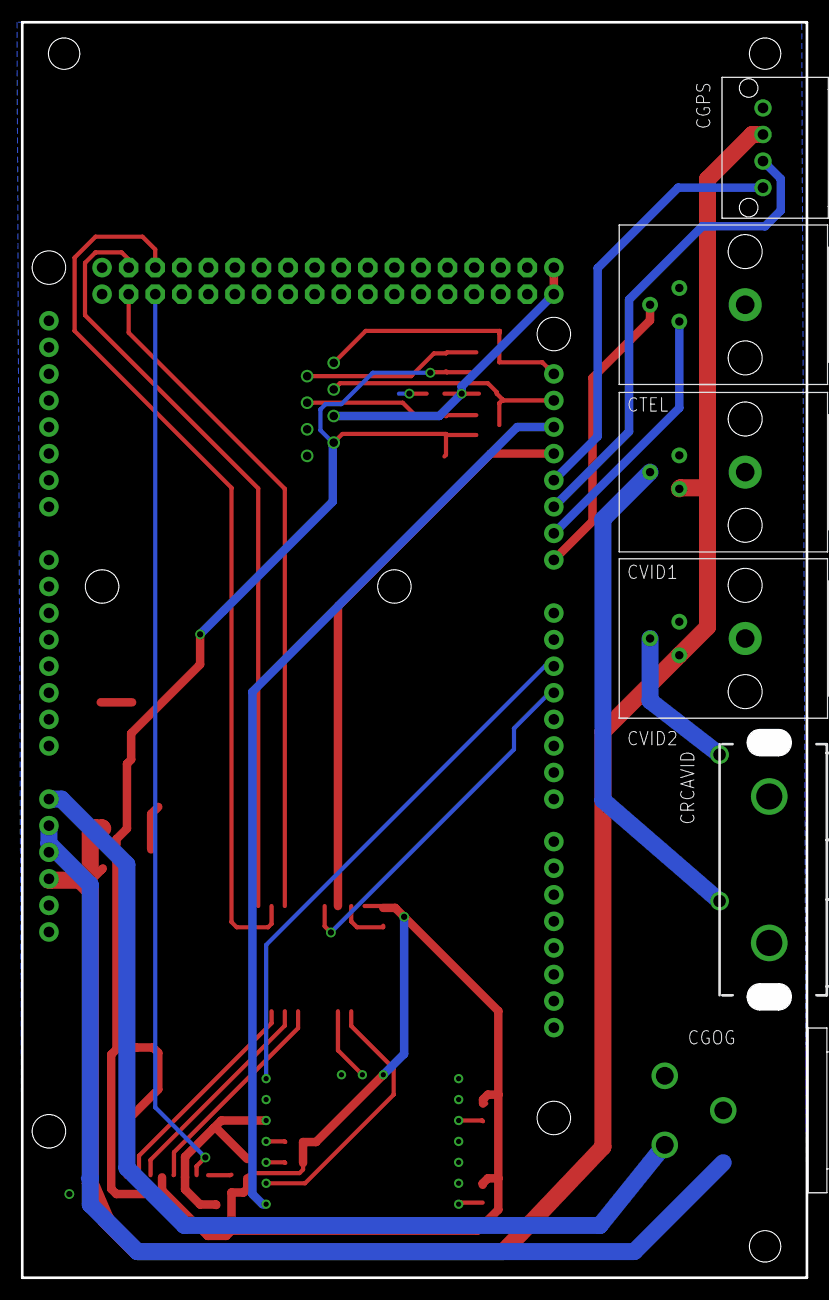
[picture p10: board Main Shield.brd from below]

Board: 2 copper layers, 75.0 x 120.0 mm, 30 parts (6 on the bottom side), 33 nets.

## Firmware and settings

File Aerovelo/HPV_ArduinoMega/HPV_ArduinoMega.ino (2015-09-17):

/* Arduino Mega Main Program
 * By Oleksiy Ryndin and Sherry Shi
 */
 
 /*
     TODO:
     
      - BUG: When simulation mode, will never enter BRAKE MODE????
     
      - Integer overflow on the simulated distance (32,000? even though it's always treated as a float)
      - And overflow on something else in the log    
      - check 45 M as the simpleDisp shown after simulation
      
      - store default calibration number (507 Hz, found in simulation.cpp also) in one place

      - GPS frequency investigation (moving average, update freq, and so on)


      Done- percent difference = (gps - simulated) / gps * 100%
      Done- check wheel circumference (based on past excel data)
  
      Done- keep only one sd card logging function (the one that takes in a filename) 
        (or do something even smarter than the current method)
      
      Done- GPS time enable  

  */


/**********************************************************************************************************************
 *                                                      LIBRARIES                                                     *
 **********************************************************************************************************************/
#include <SD.h>
#include <SPI.h>
#include <Wire.h>
#include <SFE_LSM9DS0.h>
#include "inttypes.h"
#include "ANT_interface.h"
#include "GPS_UBLOX.h"
#include "slip.h"
#include "simulation.h"

/**********************************************************************************************************************
 *                                                      PARAMETERS                                                    *
 **********************************************************************************************************************/
// ADJUSTABLE PARAMETERS
#define PERIOD 1000 // Main loop period
#define BRAKE_MODE_ENTER 50000 // When distance*1000 [m] from start coordinates is less than this, enter brake mode
#define BRAKE_MODE_EXIT 1200000 // When distance*1000 [m] from start coordinates is larger than this, exit brake mode
#define G_BM 9.79778
#define TIRE_CIRC 1.93 // Metres
#define COURSE_LENGTH   8045 // Metres  ****Change this in simulation.cpp also!!!
#define POWER_START      300 // Watts
#define POWER_PRE_SPRINT 337 // Watts
#define CALIBRATION_TIME 15000 // Milliseconds (Should be a few seconds less than the beginningPanels time, so the pedal calibration value can be seen)

//#define DRIVE_ETA 0.95 // Drivetrain efficiency
//#define M 113.85 // Mass of bike in kg
//#define M_WHEELS 2.23 // Wheel mass in kg (effective factor applied)
//#define M_TOTAL M + M_WHEELS

// BOOLEAN FLAGS
#define SERIAL_PRINT false
#define CALIBRATE true
int BRAKE_MODE = 0;
bool SIMULATION = false; // enabling simulation during a real run

/**********************************************************************************************************************
 *                                                    PERIPHERAL SETUP                                                *
 **********************************************************************************************************************/
// OSD
char slipBuffer[N_SLIP]; //SLIP.h

// ANT+
static uint8_t antBuffer[64]; // ANT+
char antFilename[32];
static uint8_t Hrt;

// SD 
char sdBuffer[128]; //SD
char logFilename[32] = "LogTest.txt"; // "LGdflt.txt"

// GPS
char gpsFilename[32];
// Default coordinates as bike room (256 McCaul Street)
int32_t LattitudeStart = 436585166, LongitudeStart = -793934912, AltitudeStart = 117689;

// Finish based on run on Monday Sept 14 (Morning)
int32_t LattitudeFinish = 404667129, LongitudeFinish = -1170625839, AltitudeFinish = 1408776;

// Finish based on coordinates from old SD card
//int32_t LattitudeFinish = 404675025, LongitudeFinish = -1170627136, AltitudeFinish = 1406018;

int32_t LattitudePrev, LongitudePrev, AltitudePrev;
int8_t startSet = 0;
uint32_t GPS_totalDistance = 0;

// Toggle Button
const uint8_t TOGGLE_PIN = A1;
int8_t lastToggle;
int8_t Toggle;
int8_t profileNum = 0;
char profileFilename[32] = {0};
char profileName[16];

// IMU setup
#define LSM9DS0_XM  0x1D 
#define LSM9DS0_G   0x6B
LSM9DS0 dof(MODE_I2C, LSM9DS0_G, LSM9DS0_XM);
//const byte INT1XM = 33; // For interrupts on accelerometer
float abias[3] = {0, 0, 0}, gbias[3] = {0, 0, 0};
float ax, ay, az, gx, gy, gz, mx, my, mz;
int accSample = 500;
#include "RunningAverage.h"
RunningAverage accAvg(accSample);

/* Hall Effect 
+5V - Yellow - RED
GND - Green - GREEN
Analog - Orange - BLUE */


/**********************************************************************************************************************
 *                                                        VARIABLES                                                   *
 **********************************************************************************************************************/
uint32_t TIME;
uint32_t TEMPTIME;
double coeff[7] = {0};

int8_t START = 0;

static float power = 0, cadence, velocity, distance = 0;
float averagePower, power10s, targetPower;
static bool coast = false;
static uint16_t time_int = 0;
static uint16_t t2 = 0;
static uint32_t lastGPSUpdate = millis();
static uint32_t targetSpeed = 0;
static int32_t displacement;
static int32_t simpleDisplacement = 0;
static int32_t accel = 0;
int32_t rando = 0;
float logDisplacement = 0;
static int32_t lat, lon, alt;
static bool GPSLost = false;

uint8_t temp;
int8_t i, m;

// Hall Effect
float vel, velAvg;
int32_t velAvgInt = 0;
int sensorValue = 0;
int count = 0;
static int32_t currentTimeFunc = 1;
static int32_t previousTimeFunc = 0;
boolean trigger = false;

static int32_t currSpeed = 0;
static int32_t prevSpeed = 0;
static int32_t prevTime = 0;
static int32_t currTime = 100;
static int32_t hallStartTime = 0;
int threshold = 288;

// Runtime
uint16_t timePlaceholder = 0;

int32_t qqq = 0;

/**********************************************************************************************************************
 *                                                         SETUP                                                      *
 **********************************************************************************************************************/
void setup() {

  timePlaceholder = millis();
  
  // Serial Setup
  Serial.begin(115200);	// COM port
  Serial3.begin(115200); // OSD
  Serial1.begin(57600);	// ANT+
  // Serial2 is GPS
  if (SERIAL_PRINT) { Serial.println("Program start!"); }
  
  // Toggle
  pinMode(TOGGLE_PIN, INPUT);
  digitalWrite(TOGGLE_PIN, HIGH); // Enables the internal pullup resistor

  // Check status of button, if HIGH simulation mode, else SIMULATION stays equal to false
  if (digitalRead(TOGGLE_PIN)) {
    SIMULATION = true; 
  }
   
  // Reset ANT+
  pinMode(3, OUTPUT);
  digitalWrite(3, LOW);
  delayMicroseconds(2000);
  digitalWrite(3, HIGH);
  delayMicroseconds(2000);

  // Initialize GPS and SD
  GPS.Init();
  //sendGPSCOMM(true);
  sd_Init();

  // Figure out SD card log iteration.
  for (int i = 1; i < 100000; ++i){
    sprintf(logFilename, "Log%d.csv", i);
    if (!SD.exists(logFilename)){
      //sprintf(SRMlogFilename, "SLg%d.csv", i);
      break;
    }
  }
  // Write the log file headings
  sd_Log("Time (hh:mm:ss), Time (ms), Displacement (m), Sim Distance (m), GPS Speed (km/h), HallEff Speed (km/h), Target Speed (km/h), Sim Speed (km/h), Power (W), Cadence (rpm), Accel Force (N), Latitude (deg), Longitude (deg), Altitude (m), Heart Rate (bpm), Battery (V), Temperature (C),");
  
  // ANT_SetupChannel(antBuffer, 0, 0, 0, 8182, 0); UNCOMMENT THIS LINE TO SEARCH FOR ANY DEVICE (ONLY SAFE FOR DEBUGGING)
  ANT_SetupChannel(antBuffer, 0, 11, 0, 8182, 12131); // Crank Torque Frequency
  ANT_SetupChannel(antBuffer, 1, 120, 0, 16140, 45063);  // Heart rate channel
  if (SERIAL_PRINT) { Serial.println("ANT+ setup complete."); }

  // Wait for at least 1000 ms from startup so the OSD receives the mode and battery level
  while (millis() - timePlaceholder < 3000) {
    delay(10);
  }

  // Placed here so there's time for the OSD to boot up
  sendMode(); // Send the mode to the OSD
  sendBattery(); 
  
  // Calibrate pedals
  if (CALIBRATE) { calibrate(); }

  // PUT OSD INTO BRAKE MODE (for testing)
//  BRAKE_MODE = 1;
//  sendBrakeMode(BRAKE_MODE);

  TIME = millis() + PERIOD; 
 
//  Serial.print("Setup ");
//  Serial.println(millis()-timePlaceholder);



// EXCESS CODE (MAY BE REQUIRED AT SOME POINT)

  // Hall effect setup
//  thresholdHallEffect(5);
//  Serial.print("threshold: ");
//  Serial.println(threshold);
  
   /* // Accelerometer setup
  uint16_t status = dof.begin();
  dof.setAccelScale(dof.A_SCALE_2G); // The smaller the range, the higher the resolution
  dof.setAccelODR(dof.A_ODR_400); // Set output data rate (ODR) at 400 Hz
  dof.setAccelABW(dof.A_ABW_50); // Anti-aliasing filter (like a low pass) at 50 Hz
  // Use the FIFO mode to average accelerometer and gyro readings to calculate the biases, which can then be removed from
  // all subsequent measurements.
  dof.calLSM9DS0(gbias, abias);
  accAvg.fillValue(0, accSample); */
  
  // For checking the battery voltage
  //analogReference(INTERNAL2V56);

  //loadFinishCoordinates();
}


/**********************************************************************************************************************
 *                                                      MAIN PROGRAM                                                  *
 **********************************************************************************************************************/
void loop() {
 
/*********************** BEGIN: PERIOD WHILE LOOP ***************************/  
 
  while (TIME > millis()) {
    
    //receiveOSD() // Should print messages received from OSD?
    
    if (BRAKE_MODE) {
      
      //timePlaceholder = millis();
      
      currSpeed = (int32_t)(hallSpeed(850, 1)*100000000); // m/s scaled up by 1E8 // 500ms gives clean data above 60km/h
      // time is in micro seconds (scaled up by 1E6)
      // NOTE: using currentTimeFunc which is updated at the end of the hallSpeed call
      accel = (currSpeed - prevSpeed) / (currentTimeFunc - prevTime); // Result is m/s^2 scaled up by 1E2

      prevTime = currentTimeFunc;
      prevSpeed = currSpeed;  

//      Serial.print("Current Time [micro s]: ");
//      Serial.println(currentTimeFunc);
//      Serial.print("Previous Time [micro s]: ");
//      Serial.println(prevTime);
//      Serial.print("Speed [km/h]: ");
//      Serial.print(float(currSpeed*3.6)/100000000);
//      Serial.print("    Accel Force [N]: ");
//      Serial.println(accel*105/100);
      
      sendAccel();
      //sendSpeed();

     
    //Serial.print("BRAKE MODE     ");
    //Serial.println(millis()-timePlaceholder); 
    }
    
/************************* BEGIN: NOT BRAKE MODE ****************************/
    else {     
      //timePlaceholder = millis();
/*********************** BEGIN: READ ANT+ DATA ***************************/
      if (Serial1.available()) {
        if ((m = receiveANT(antBuffer)) > 0) {
          if (SERIAL_PRINT) { 
            Serial.print("ANT+ Packet Received: ");
            for (i = 0; i < m + 3; ++i) {
              Serial.print(antBuffer[i], HEX);
              Serial.print(' ');
            } Serial.print('\n');
          }
          if (m == 9) {
            switch (antBuffer[2]) { // Channel
              case 0: // Power meter
                readPowerMeter(antBuffer, 0, &time_int, &power, &cadence, &coast);
                
                if (!coast && power != 0 && time_int != 0) {
                  simulate(power, time_int, 2, &velocity, &distance);
                  t2 = millis();	// last power meter data message received
                } else if (coast) {
                  simulate(0, 2 * (millis() - t2) , 0, &velocity, &distance);
                  t2 = millis();
                }
                if (power > 0.1) { // Ignore power values of 0
                  averagePower = pwrAvg(power);
                  power10s = tenSecPower(power);
                }
                sendPower();	  
                logData(); // Write the updated values to the log file (mainly power updates)
                break;
  
              case 1: // Heart rate.
                Hrt = antBuffer[3 + 7];
                sendHeartRate();
                break;
            }
          }
        }
      }    
/************************* END: READ ANT+ DATA **************************/


/*********************** BEGIN: READ GPS DATA ***************************/
      doGPS();
/************************* END: READ GPS DATA ****************************/


    }
/************************* END: NOT BRAKE MODE ****************************/
 


  }
/*********************** END: PERIOD WHILE LOOP ***************************/ 

  TIME += PERIOD;
  
  //timePlaceholder = millis();
  logData();  
  //Serial.print("LogData        ");
  //Serial.println(millis()-timePlaceholder);
}



/*********************************************************************************
 *                               FUNCTIONS
 *********************************************************************************/

// Logging data to the SD card
void logData() {
  //   sd_Log("Time (hh:mm:ss), Time (ms), Displacement (m), Sim Distance (m), GPS Speed (km/h), HallEff Speed (km/h), Target Speed (km/h), Sim Speed (km/h), Power (W), Cadence (rpm), Accel Force (N), Latitude (deg), Longitude (deg), Altitude (m), Heart Rate (bpm), Battery (V), Temperature (C),");
  
  sd_Open(logFilename);
  
  // Times
  sd_Print("\r\n");
  sprintf((char*)sdBuffer, "%u:%u:%u, ", GPS.UTC.hour, GPS.UTC.minute, GPS.UTC.second);
  sd_Print(sdBuffer);
  sd_Print(dtoa(sdBuffer, (double)millis())); sd_Print(", ");

  // Distances
  sprintf((char*)sdBuffer, "%d, ", simpleDisplacement/ 1000);
  sd_Print(sdBuffer);  
  sd_Print(ftoa(sdBuffer, distance, 3)); sd_Print(", ");

  // Speeds
  sd_Print(dtoa(sdBuffer, GPS.Ground_Speed*0.036)); sd_Print(", ");
  sd_Print(dtoa(sdBuffer, velAvg*39/18.0*3.6)); sd_Print(", ");
  sd_Print(dtoa(sdBuffer, targetSpeed*0.036)); sd_Print(", ");  
  sd_Print(dtoa(sdBuffer, velocity * 3.6)); sd_Print(", ");
 
  // Power and Cadence
  sd_Print(dtoa(sdBuffer, power)); sd_Print(", ");
  sd_Print(dtoa(sdBuffer, cadence)); sd_Print(", ");
  
  // Accel Force
  sd_Print(dtoa(sdBuffer, float(accel)*105/100)); sd_Print(", ");
//  Serial.print("debug accel: ");
//  Serial.println(float(accel)*105/100);
 
  // GPS Coordinates
  sd_Print(dtoa(sdBuffer, lat*1.0 / 10000000)); sd_Print(", ");
  sd_Print(dtoa(sdBuffer, lon*1.0 / 10000000)); sd_Print(", ");
  sd_Print(dtoa(sdBuffer, alt*1.0 / 1000));     sd_Print(", ");
 
  // Heart rate and battery
  sprintf(sdBuffer, "%u, ", Hrt);
  sd_Print(sdBuffer);
  sd_Print(ftoa(sdBuffer, getBatteryLevel(), 4)); sd_Print(", ");
  sd_Print(ftoa(sdBuffer, readTemp(), 4)); sd_Print(", ");
  
  sd_Close();
}


// Calibrating the pedals
void calibrate() {
  bool calibrated = false;
  int8_t m;
  uint8_t i = 0; // Index for cal_values
  int16_t cal_values[6];
  int16_t calibrationValue;

  Serial.println("Begin calibration... Waiting for calibration messages.");
  sd_Log("Begin calibration... Waiting for calibration messages.");
  calibrateMessageOSD(1, 0);

  TEMPTIME = millis(); //To timeout the calibration if taking too long
  
  while (i < 6) {
    if (Serial1.available() && (m = receiveANT(antBuffer)) == 9 && antBuffer[1] == 0x4E && antBuffer[4] == 0x10) {
      cal_values[i++] = antBuffer[9] * 256 + antBuffer[10];
      calibrateMessageOSD(2, 0);
      Serial.print("Receiving... ");
      sprintf(sdBuffer, "Received message %d. ", i);
      sd_Log(sdBuffer);
      
      // Should mean that all the required calibrated values were received
      if (i == 6) {
        calibrated = true; }   
    }
    else { // Nothing available on the ANT serial
      if (millis() - TEMPTIME > CALIBRATION_TIME) { // If more than CALIBRATION_TIME already passed
        break; // exit the while loop
      }
    }
  }
  
  if (calibrated) { 
    calibrationValue = average(cal_values, 6);
    setOffset(calibrationValue);
  
    Serial.print("Calibration complete! Offset is: ");
    Serial.print(calibrationValue);
    Serial.println(" Hz");
    sprintf(sdBuffer, "Calibration complete! Offset is: %d Hz. ", calibrationValue);
    sd_Log(sdBuffer);
    
    // Display the calibration data on the OSD
    calibrateMessageOSD(3, calibrationValue); // The number 3 writes the value to the screen (See calibration state in OSD_panels_HPV) 
  }
  
  else {
    calibrationValue = 507;
    Serial.println("Calibration timed-out...Offset is set as default: 507 Hz");
    sprintf(sdBuffer, "Calibration timed-out...Offset is set as default: 507 Hz");
    sd_Log(sdBuffer);
    
    // Display the calibration data on the OSD
    calibrateMessageOSD(4, calibrationValue); // The number 4 write default to the screen (See calibration state in OSD_panels_HPV)
  }
  // Wait and then clear up the screen (IF REQUIRED)
  //delay(3000); // Not large enough? seeing flicker?
  //calibrateMessageOSD(0, calibrationValue); // The number 0 writes a blank message to the screen 
}


// Sends the specified message and value to the OSD
void calibrateMessageOSD(uint8_t messageNum, int16_t calibrationValue) {
  *((uint8_t*)slipBuffer + 0) = ID_CALIBRATION;
  *((uint8_t*)(slipBuffer + 1 + 0)) = messageNum;
  *((int16_t*)(slipBuffer + 1 + 1)) = calibrationValue;
  *((uint8_t*)slipBuffer + 1 + 3) = 0;
  SlipPacketSend(4, (char*)slipBuffer, &Serial3);
}

// Gets the threshold for the hall effect sensor
void thresholdHallEffect(int N) {
  
  int sensorValue;
  int sensorMin = threshold;
  int sensorMax = threshold;
  boolean trigger= false;
  int i = 0;
  
  while (i < N) {
  sensorValue = analogRead(A3);
  //Serial.println(sensorValue);
  if ((sensorValue < threshold) && (trigger == 0)) {
    trigger = 1;
    i++;
    Serial.print(i);
    Serial.print('\t');
    Serial.println(2);
  }
  else if ((sensorValue > threshold) && (trigger == 1)) {
    trigger = 0;
  }
  if (sensorValue < sensorMin)
    sensorMin = sensorValue;
  else if (sensorValue > sensorMax)
      sensorMax = sensorValue;
  }
  
  threshold = (sensorMax + sensorMin)/2;
  
}

float hallSpeed(int sampleTime, int samples) {
   
    count = 0; // How many velocity points accumulated
    velAvg = 0;

    hallStartTime = millis();
   
    //Serial.println("entered hallSpeed");
//    while (millis() - hallStartTime < sampleTime) {     
    while (count < samples+1) {
          
      if (millis() - hallStartTime > sampleTime) {
        break;
      }
      
      sensorValue = analogRead(A3);
      //Serial.println(sensorValue);
        
      if ((sensorValue < threshold) && (trigger == 0)) {
        currentTimeFunc = micros();
          
          // Ignore the first trigger to get timing correctly
          if (count != 0) {
            vel = TIRE_CIRC/(currentTimeFunc-previousTimeFunc)*1000000;  
            velAvg = velAvg + vel;
            
//            Serial.print(currentTimeFunc);
//            Serial.print('\t');
//            Serial.print(vel);
//            Serial.print('\t');
//            Serial.print(count);
//            Serial.print('\t');
//            Serial.println(3);
          }
        trigger = 1;
        previousTimeFunc = currentTimeFunc;
        count++;
      }
      
      else if ((sensorValue > threshold) && (trigger == 1)) {
        trigger = 0;
      }
      
      
//      currentTimeFunc = micros();
//    timePlaceholder = millis();
      doGPS();
//    Serial.print("doGPS took: ");
//    Serial.println(millis() - timePlaceholder);
      
      
      

    }
    
//    Serial.println(3);
//    Serial.print("Collected ");
//    Serial.print(count);
//    Serial.print(" samples, velAvg = ");
//    Serial.print(velAvg/count);


    
    if (count == 0) {
      //Serial.println("Zero - bad avg...");
      return 0; 
  }
    else { 
      velAvgInt = (int32_t)(velAvg*100*39/18)/(count - 1); // m/s becomes 100 m/s and 39-18 gear reduction
      // Check gear ratio
      // Check wheel circumference
      // Check cadence and gear and speed correlation.

      return velAvg*39/18/(count - 1); 
    }    

}
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

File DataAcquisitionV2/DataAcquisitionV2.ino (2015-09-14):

/*
 Data Acquisition V2
 
 Created 25 August 2015
 by Alex Selwa
 
 */
 
// Set up infrared
#include <Wire.h>
#include <Adafruit_MLX90614.h>
Adafruit_MLX90614 mlx = Adafruit_MLX90614();

// Set up thermocouple instance with software SPI on any three digital IO pins.
#include <SPI.h>
#include "Adafruit_MAX31855.h" 
#define DO   4
#define CS   5
#define CLK  6
Adafruit_MAX31855 thermocouple(CLK, CS, DO);
 
// Set up O2 and CO2 sensor
#include <math.h>
#include <SoftwareSerial.h>
int const pinO2 = A0; // analog pin used to connect the O2 sensor
const int pinRx = 8;
const int pinTx = 7;
SoftwareSerial K_30_Serial(pinTx,pinRx);
int valMultiplier = 1; 
byte readCO2[] = 
  {0xFE, 0X44, 0X00, 0X08, 0X02, 0X9F, 0X25};
byte response[] = {0,0,0,0,0,0,0};  //create an array to store the response 

// Open Log Setup   
//int resetOpenLog = 2;
#include <SoftwareSerial.h>
//Connect TXO of OpenLog to pin 3, RXI to pin 2
SoftwareSerial OpenLog(3, 2); //Soft RX on 3, Soft TX out on 2
//SoftwareSerial(rxPin, txPin)
char buff[80];
//int resetOpenLog = 1;
//pinMode(resetOpenLog, OUTPUT);

      // ADJUST THESE PARAMETERS    
      int period = 300; // ms      
      float number_of_points = 10; //for initial O2 average

// Flow controlling variables
unsigned long time;
int counter = 0; // For averaging while loop

// Temporary variables used
float O2_temp;
float CO2_temp;
float caliper_temp;
float disk_temp;
float disk_amb_temp;
unsigned long valCO2 = 0;
float meanO2 = 0;
    
    
    
void setup() {
  // Open Log setup
  //pinMode(resetOpenLog, OUTPUT);
  //Serial.begin(115200);
  OpenLog.begin(9600);
  
//  //Reset OpenLog
//  digitalWrite(resetOpenLog, LOW);
//  delay(100);
//  digitalWrite(resetOpenLog, HIGH);
//
//  //Wait for OpenLog to respond with '<' to indicate it is alive and recording to a file
//  while(1) {
//    if(Serial.available())
//      if(Serial.read() == '<') break;
//  }
  
  

  //start the reading of the co2 sensor
  K_30_Serial.begin(9600);
  
  // IR temperature sensor setup
  mlx.begin();
  
//  // Calibrate O2 Sensor
//  for (int i=0; i < number_of_points; i++){
//    meanO2 = meanO2 + analogRead(pinO2);
//    // print out the values to the serial monitor
//    //Serial.println(analogRead(pinO2));
//    delay(400);
//  } 
//  meanO2 = meanO2/number_of_points;
//    
//  sprintf(buff, "Initial average O2: ");
//  ftoa(buff, meanO2, 3);
//  OpenLog.print(buff);
//  OpenLog.println(",");
//  Serial.print(buff);
//  Serial.println(",");
  
  sprintf(buff, "Time [s], O2 [raw], CO2 [ppm], Caliper [deg C], Disk[deg C], Ambient [deg C],");
  OpenLog.println(buff);
  //Serial.println(buff);
}


int valO2 = 0;



// Measurement and Printout Loop
void loop() {
  
  // Reset these "accumulator" variables
  O2_temp = 0;
  CO2_temp = 0;
  caliper_temp = 0;
  disk_temp = 0;
  disk_amb_temp = 0;
  counter = 0;
  time = millis();
  
   

  
  while ((millis() - time) < period) {
 
    
    //sprintf(buff, " Just entered while loop, time: %d", time);
    //OpenLog.println(buff); //regular println works with v2.51 and above
    
    
    // O2
    valO2 = analogRead(pinO2);
    O2_temp = 0; // Commented since sensor removed: O2_temp + valO2; // read the value of the O2 sensor
    
    // CO2  
    sendRequest(readCO2); 
    delay(50);
    if (getValue(response) < 10001) {
      valCO2 = getValue(response);
    }
    else {
      //valCO2 = CO2_average[e.datapoint]/i; // Divide by zero?
      valCO2 = 10000; 
    }
    CO2_temp = CO2_temp + valCO2;   
    
    
    // Caliper temp
    caliper_temp = caliper_temp + thermocouple.readCelsius();
    // Disk temp
    disk_temp = disk_temp + mlx.readObjectTempC();
    // Ambient temp
    disk_amb_temp = disk_amb_temp + mlx.readAmbientTempC();
    // Averaging counter
    counter++;
    //sprintf(buff, "End of while, counter: %d.txt", counter);
    //OpenLog.println(buff); //regular println works with v2.51 and above
  }
  

  //sprintf(buff, "Time+period: %d, ", (int)(time+period));
  //sprintf(buff, "%d, %d, %d, %d, %d, %d,", (int)(time+period), (int)(O2_temp/counter*100), (int)(CO2_temp/counter*100), (int)(caliper_temp/counter*100), (int)(disk_temp/counter*100), (int)(disk_amb_temp/counter*100));
  //OpenLog.println(buff);

  // Write to Open Logger  
  ftoa(buff, (time+period)/1000, 3);
  OpenLog.print(buff);
  OpenLog.print(", ");
  
  //Serial.print(buff);
  //Serial.print(", ");

  ftoa(buff, O2_temp/counter, 3);
  OpenLog.print(buff);
  OpenLog.print(", ");

  //Serial.print(buff);
  //Serial.print(", ");  

  ftoa(buff, CO2_temp/counter, 3);
  OpenLog.print(buff);
  OpenLog.print(", ");
  
  //Serial.print(buff);
  //Serial.print(", ");

  ftoa(buff, caliper_temp/counter, 3);
  OpenLog.print(buff);
  OpenLog.print(", ");
  
  //Serial.print(buff);
  //Serial.print(", ");

  ftoa(buff, disk_temp/counter, 3);
  OpenLog.print(buff);
  OpenLog.print(", ");
  
  //Serial.print(buff);
  //Serial.print(", ");

  ftoa(buff, disk_amb_temp/counter, 3);
  OpenLog.print(buff);
  OpenLog.println(", ");
  
  //Serial.print(buff);
  //Serial.println(", ");
  
  
 }
 
 
/**************************************************************
 *                      FUNCTIONS                             *
 **************************************************************/


char *ftoa(char *a, double f, int precision)
{
 long p[] = {0,10,100,1000,10000,100000,1000000,10000000,100000000};
 
 char *ret = a;
 long heiltal = (long)f;
 itoa(heiltal, a, 10);
 while (*a != '\0') a++;
 *a++ = '.';
 long desimal = abs((long)((f - heiltal) * p[precision]));
 itoa(desimal, a, 10);
 return ret;
}



//function for reading the UART co2 sensor
void sendRequest(byte packet[]) 
{ 
  while(!K_30_Serial.available())  //keep sending request until we start to get a response 
  { 
    K_30_Serial.write(readCO2,7); 
    delay(25); 
  } 
   
  int timeout=0;  //set a timeout counter 
  while(K_30_Serial.available() < 7 )    //Wait to get a 7 byte response 
  { 
    timeout++;   
    if(timeout > 10)    //if it takes to long there was probably an error 
      { 
        while(K_30_Serial.available())  //flush whatever we have 
          K_30_Serial.read(); 
           
          timeout = 0;   
          break;                        //exit and try again 
      } 
      delay(25); 
  } 
   
  for (int i=0; i < 7; i++) 
  { 
    response[i] = K_30_Serial.read(); 
  }   
} 

unsigned long getValue(byte packet[]) 
{ 
    int high = packet[3];                        //high byte for value is 4th byte in packet in the packet 
    int low = packet[4];                         //low byte for value is 5th byte in the packet 

    unsigned long val = high*256 + low;                //Combine high byte and low byte with this formula to get value 
    return val* valMultiplier; 
} 

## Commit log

2014-07-16 Inital commit - add all the files
    [ElevData.csv]
2014-07-16 working on elevation power calculations
    working on elevation power calculations
2014-07-16 Revert "Replaced ANT_interface2"
    This reverts commit 952588fa785ceab49986b3ebbc41c79809ae3066.
    [ANT_interface2.ino]
2014-07-16 file does not work
    attempted to fix the Pelev calculations but positive feedback screws up
    whole calculation
    [ANT_interface2.ino]
2014-07-18 changed Pelev
    attempted to correct Pelev calculations, untested
    [ANT_interface2.ino]
2014-07-18 Integrated code from the ANT interface with OSD and ArduinoMega code
2014-07-23 Added some print statements to test the GPS
2014-07-23 Minor changes to UBLOX and HPV_ArduinoMega for debugging: mostly print statements
2014-07-25 OSD now displays distance travelled based on GPS measurements. No filtering applied. Currently set up to NOT use SD card info.
2014-07-30 Revert "Heart meter now outputting"
    This reverts commit dd00149cfb93f6b963a563ea873c792e10c9e075.
    [HPV_ArduinoMega.ino]
2014-07-30 Revert "Revert "Heart meter now outputting""
    This reverts commit 8f9f0e41a259e8cc47af1755d671c3c69bd85e2c.
    [HPV_ArduinoMega.ino]
2014-07-30 fixed ANT+ for power meter and heart meter
    blah
    [ANT_interface.cpp, ANT_interface2.ino, HPV_ArduinoMega.ino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]
2014-07-30 Power updates properly on the OSD now, but power calculation is invalid coming out of a coast (not sure if this error was recently introduced or not)
    [HPV_ArduinoMega.ino, simulation.cpp]
2014-07-31 fixed displaying of variables
    [HPV_ArduinoMega.ino, OSD_panels_HPV.ino, simulation.cpp]
2014-08-04 Disabled first calculation after coming out of a coast: the program no longer shows a spike in velocity, power, distance, etc. Also fixed the distance display to output in metres (not km)
    [HPV_ArduinoMega.ino, simulation.cpp]
2014-08-04 Realized that simulation was not working: velocity peaked out at 30km/h. Changed algorithm back to non-iterative approach and it worked fine
    [HPV_ArduinoMega.ino, OSD_panels_HPV.ino, simulation.cpp]
2014-08-04 Added calibration at the beginning of the program and a new panel for it on the display. Not yet tested.
2014-08-06 Fixed some ANT buffer overflow things and changed the simulation back to iterative (max 2 iterations)
    [ANT_interface.cpp, HPV_ArduinoMega.ino, simulation.cpp]
2014-08-06 added powercalc file
    to compare parameters
2014-08-10 Added battery voltage display to OSD and fixed the simulation to run properly with multiple iterations. Target speed isn't quite right yet.
    [HPV_ArduinoMega.ino, HPV_OSD.ino, OSD_SLIP.h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]
2014-08-11 Fixed target speed to work properly
    [HPV_ArduinoMega.ino, simulation.cpp]
2014-08-11 Forgot to add the battery file
2014-08-11 Changed code to use analog 2 for battery readings. OSD displays GPS transmission warnings when it stops sending data
2014-08-15 Properly configured the distance to go variables and fixed an error (geographic coordinates were previously declared as unsigned)
    [HPV_ArduinoMega.ino, OSD_panels_HPV.ino]
2014-08-18 Changes to logging and OSD panels. After getting pedals back on the bike, simulation was discovered to behave strangely. Old errors are present again, such as velocity spiking to infinity while coast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
    [HPV_ArduinoMega.ino, OSD_panels_HPV.ino, simulation.cpp]
2014-08-19 Found the root of the velocity problems (I think). Added a check guard for CdA to see if it becomes NaN, which should stop the error.
    [HPV_ArduinoMega.h, HPV_ArduinoMega.ino, HPV_OSD.ino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]
2014-08-19 Added more error-checking in simulate for invalid values. Added support for poewr only messages to be compatible with Vector (untested).
    [HPV_ArduinoMega.ino, HPV_OSD.ino, simulation.cpp]
2014-08-22 Changed some logging things and the battery pin.
2014-08-25 temperature testing
    added code for temperature sensor testing, use function readTemp()
2014-08-25 update temperature testing
    added comments, removed function input variable
2014-08-25 Added OSD support for 10s moving power average and target poewr
2014-08-25 Added in target power and average power displays
2014-08-26 Minor fixes to power averaging behaviour: fixed division by zero in pwrAvg and made program skip averaging if power is 0W (otherwise it starts averaging as soon as you switch profiles)
    [HPV_ArduinoMega.ino, HPV_OSD.ino, OSD_SLIP.h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]
2014-08-27 Changes to pins used for measuring values. Also changed the baud rate for the antenna back to what it really was and should have been
2014-08-27 Added temperature warning to OSD and started implementing battery warning
2014-08-27 Finished implementing battery and temperature OSD. Both use artificial thresholds.
2014-08-27 Corrected the battery and temperature displays. Added some documentation to the repository.
    [ANT_interface.cpp, HPV_ArduinoMega.ino, OSD_panels_HPV.ino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]
2014-09-01 Changed some pins to their correct new locations.
    [HPV_ArduinoMega.ino]
2014-09-01 Cleaned up all the code to get rid of useless commented stuff. Also implemented power target for real-time mode and fixed OSD text on profiles so it wouldn't cut into the low battery warning. Everyth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
    [ANT_interface.cpp, BOOT_Func.ino, HPV_ArduinoMega.ino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]
2014-09-06 Corrected inconsistency with the type of "displacement" when it is sent in the slip buffer (signed vs. unsigned)
    [HPV_ArduinoMega.ino]
2014-09-07 Fixed two inconsistencies with the type of variable "displacement"
    [HPV_ArduinoMega.ino]
2014-09-07 Changed the time to wait before resetting the GPS if the connection is lost
    [HPV_ArduinoMega.ino]
2014-09-07 The "unit" conversion doesn't work after the cos
    Dividing by 10000 needs to be done before cosine is applied since it
    isn’t a linear function
2014-09-09 GPS math fix and calibrate enabled
    [HPV_ArduinoMega.ino]
2014-09-10 Added support for an additional log file that writes whenever new power messages are received.
2014-09-27 Added Log files from BM2014
    [Elevation.xlsx, LOG1.CSV, LOG10.CSV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]
2014-09-28 File Management
    [Main Shield.brd, OSD Shield.brd]
2014-09-29 More File Rearranging
    [Main Shield.sch, OSD Shield.sch]
2015-08-17 Update README to explain current branches
2015-08-18 Added timeout to pedals calibration, and started implementing separate screen at beginning
2015-08-18 Working Road Testing Version
    Includes new calibration, minor fixes, updates, etc. The OSD displays
    displacement from the starting location, which is taken when the unit
    is turned on.
    [HPV_ArduinoMega.h, HPV_ArduinoMega.ino, HPV_OSD.ino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]
2015-08-24 Latest Used Version
    Note the n_average parameters and DATA_SIZE. Also it now requires a
    capacitor over the reset pin to prevent serial monitor reset. (But
    can’t flash with the capacitor connected)
    [O2CO2_Sensor4.ino]
2015-08-24 Some updates for logging including stream down print statements for more data logging
2015-08-30 Large Changes, organizing flow and separating more into other files
2015-08-31 Accelerometer and general structure changes
2015-09-01 Working accelerometer and OSD
2015-09-03 Working hall sensor and several other changes
2015-09-05 Simulation fixes and hall effect integration
    [DistanceToFinish (Slope).csv, GPSconfig2014.txt, Pdrag (Speed).csv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]
2015-09-14 Plenty of changes, but working alright just before qualifers
    [2ndLast.CSV, DistanceToFinish (Slope).csv, ElevData.csv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]
2015-09-17 Fixed target speed profile and power profile, braking bar updated
    (SD card problem gone, and speed profile gone)
    [LOG1.CSV, LOG10.CSV, LOG100.CSV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]
2015-09-18 Save before adjusting OSD and power profiles
    [Eve.CSV, EveMain.CSV, LOG6.CSV]

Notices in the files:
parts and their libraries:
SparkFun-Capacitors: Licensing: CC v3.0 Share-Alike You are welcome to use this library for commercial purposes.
